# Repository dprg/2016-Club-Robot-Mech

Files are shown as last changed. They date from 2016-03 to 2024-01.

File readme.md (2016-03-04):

# DPRG Club Robot - 2016

This GIT repository contains the design files of the mechanical parts used in DPRG's 2016 version of the club's robot.

The purpose of the robot is to provide a simple, flexible, and sturdy chassis with good components that can grow with the member's skills.

The robot is designed to be able to participate in most of DPRG's indoor competitions. 

The repository includes Inkscape files for laser cut parts, and Design Spark Mechanical and .stl files for 3D printed parts.

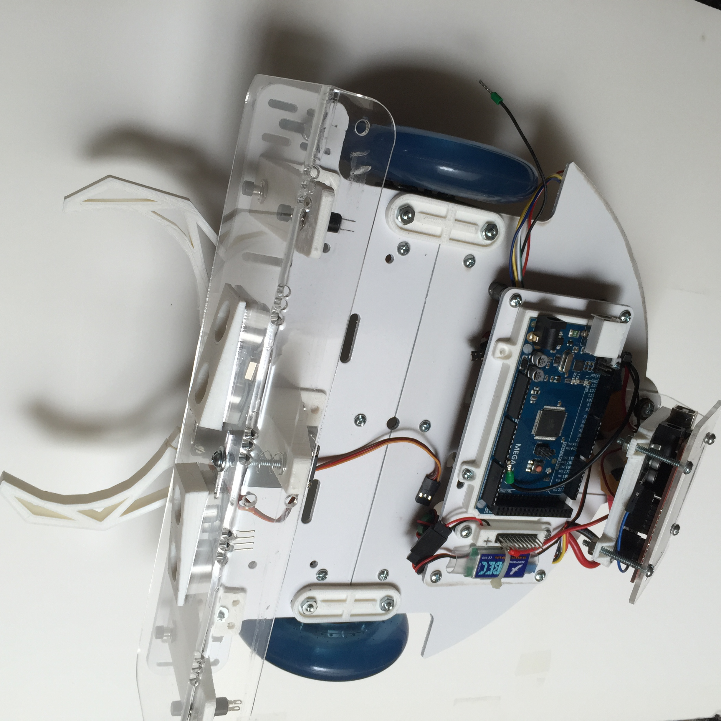
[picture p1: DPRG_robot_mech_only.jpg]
DPRG Robot - Mechanical Parts


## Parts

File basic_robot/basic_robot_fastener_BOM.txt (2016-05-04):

Basic Club Robot (version 2016) Fasteners BOM

Quality     Description
-------    --------------------------
   2       M3-0.5x6mm flat head screws
   2       4-40x3/8" screws
   4       4-40x1/2" Nylon screws
   2       4-40x3/4" screws
  24       6-32x1/2" screws
   9       6-32x3/4" screws
   4       6-32x1"   screws
   3       6-32x1-1/2" screws
   4       6-32x1-1/2 Nylon screws
   1       6-32x2-1/4" screws
   4       8-32x1"   screws
   
   4       4-40 nuts
  47       6-32 nuts
   3       6-32 lock nuts
   4       6-32 Nylon nuts
   4       8-32 nuts
   
   8       #6 washers

3D Printed Hubs

Quality     Description
-------    --------------------------
   6       4-40x3/4" screws
   4       6-32x5/16 set screws

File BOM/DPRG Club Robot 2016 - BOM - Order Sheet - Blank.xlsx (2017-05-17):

BOM for DPRG Club Robot - 2016 |  |  |  | Name -> | <enter your name>
CkBox My Order [x] | Description | Qty | Each | Baseline Cost (all options) | My Order | Comment
 |  |  |  | $196.00 | $178.00
x | Set of laser cut parts | 1 | $6.00 | $6.00 | $6.00
 | (base, motor/wheel, deck, bumper,
 | caster plate, display,
 | stand offs (20))
x | Set of 3D printed parts - PLA | 1 | $8.00 | $8.00 | $8.00
 | (bumper(3), base (2), claw,
 | buss (2), uno plate, mega plate,
 | USB guard, ultrasonic (2), fuse
 | guard, male pin protectors (2),
 | hubs (2))
x | Caster | 1 | $4.00 | $4.00 | $4.00
x | Screw/nut set | 1 | $6.00 | $6.00 | $6.00
x | Bumper springs | 2 | $1.00 | $2.00 | $2.00
x | Priming of base & deck parts | 1 | $3.00 | $3.00 | $3.00 | optional
x | Bumper switches - NC | 4 | $0.50 | $2.00 | $2.00
x | On/Off switch | 1 | $1.00 | $1.00 | $1.00
x | Wheels - 100 mm | 2 | $4.00 | $8.00 | $8.00
x | Pololu Hubs | 2 | $5.00 | $10.00 | $10.00 | optional
x | Motors with encoders | 3 | $10.50 | $21.00 | $31.50 | indicate speed (100 RPM or 200 RPM)
 | ( std - 100 RPM @ 6V) |  |  |  |  | 100 RPM
 | ( fast - 200 RPM @ 6V)
x | Set of jumpers - Dupont plugs | 1 | $6.00 | $6.00 | $6.00
 | (mix of m/m, m/f, f/f)
x | Misc wire | 1 | $1.00 | $1.00 | $1.00
x | Terminals - double row, 100 mil | 2 | $1.00 | $2.00 | $2.00
x | UBEC – 5V | 1 | $6.00 | $6.00 | $6.00
x | XT60 terminal set - m & f | 2 | $1.00 | $2.00 | $2.00
x | Resettable Fuse - 5A PPTC | 1 | $1.00 | $1.00 | $1.00
x | 2.4" TFT Display Shield | 1 | $6.00 | $6.00 | $6.00
x | Ultrasonic sensors - HC-SR04 | 2 | $1.00 | $2.00 | $2.00
x | IR sensor - non-modulated | 2 | $1.00 | $2.00 | $2.00
x | IR sensor – modulated | 3 | $2.00 | $6.00 | $6.00
x | Hobby servo - std size | 1 | $6.00 | $6.00 | $6.00
x | MonsterMoto motor driver clone | 1 | $10.00 | $10.00 | $10.00
x | Arduino power plug | 1 | $1.00 | $1.00 | $1.00
x | Arduino Uno clone | 1 | $6.50 | $6.50 | $6.50
x | Arduino Mega2560 clone | 1 | $11.00 | $11.00 | $11.00 | or Nucleo
 | Nucleo STM32F411 | 1 | $11.00 | $11.00 | $0.00 | or Mega
x | Battery LiPo - 11.1V, 2.2KmAh | 1 | $16.00 | $16.00 | $16.00 | or NiMH
 | Battery NiMH - 9.6V, 2.2KmAh | 1 | $17.50 | $17.50 | $0.00 | or LiPo
x | Nucleo Breakout board and parts | 1 |  |  | $0.00
 | (designed by Ron Grant)
x | PayPal Fees | 1 | $2.00 | $2.00 | $2.00
x | Contingency Fund | 1 | $10.00 | $10.00 | $10.00
 | (shipping, unexpected price change)

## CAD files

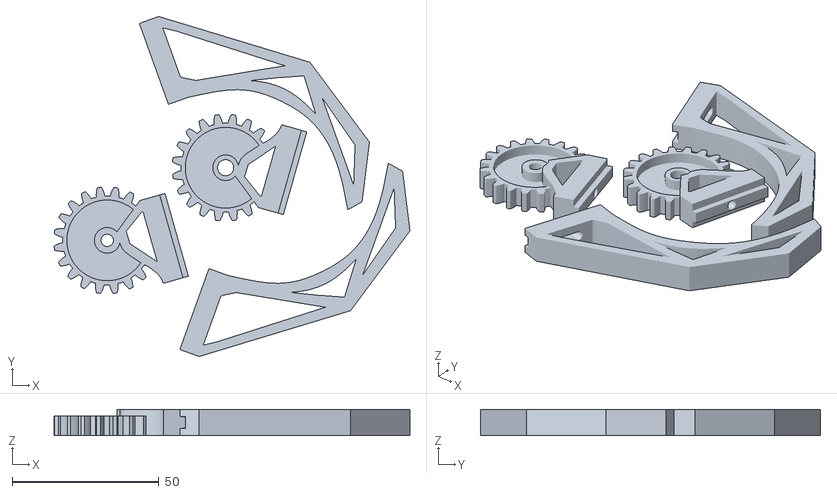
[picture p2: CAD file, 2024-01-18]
basic_robot/3d_print_parts/robot_claw_revised-1.stl
121.3 x 115.9 x 9.00

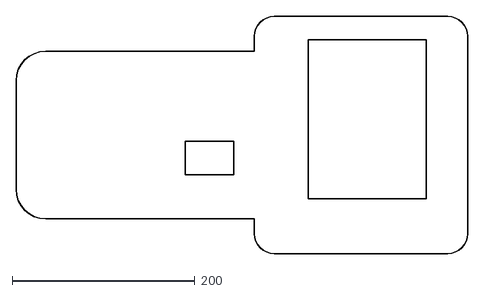
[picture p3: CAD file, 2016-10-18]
basic_robot/laser_cut_parts/display_support.dxf
494.2 x 259.4

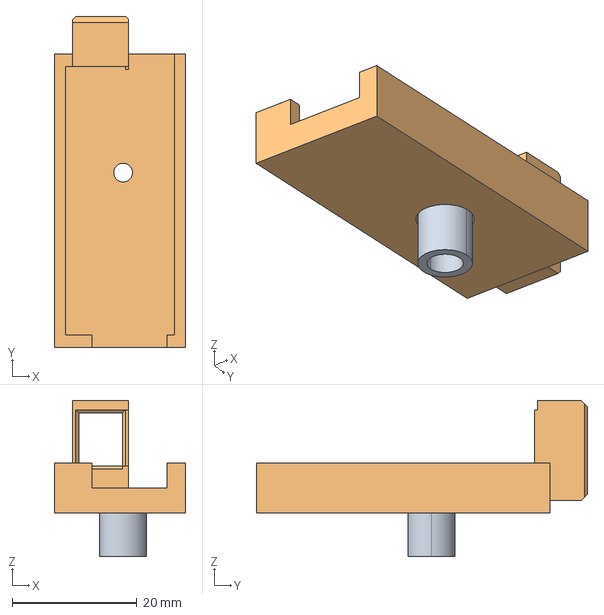
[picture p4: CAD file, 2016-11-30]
optional_parts/3d_print_parts/KeyesIr_Mount.stp
21.0 x 53.0 x 25.0 mm
Mount
Platform

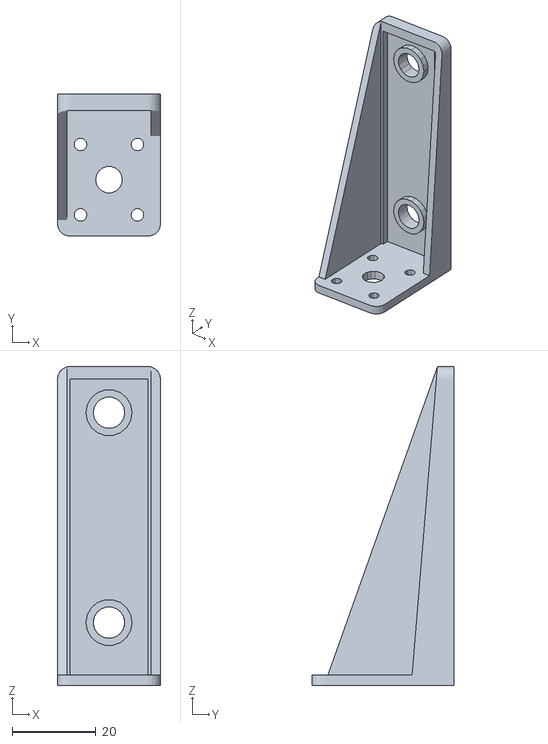
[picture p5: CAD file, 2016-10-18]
basic_robot/3d_print_parts/bumper_switch_support_left.stl
24.6 x 33.9 x 76.0

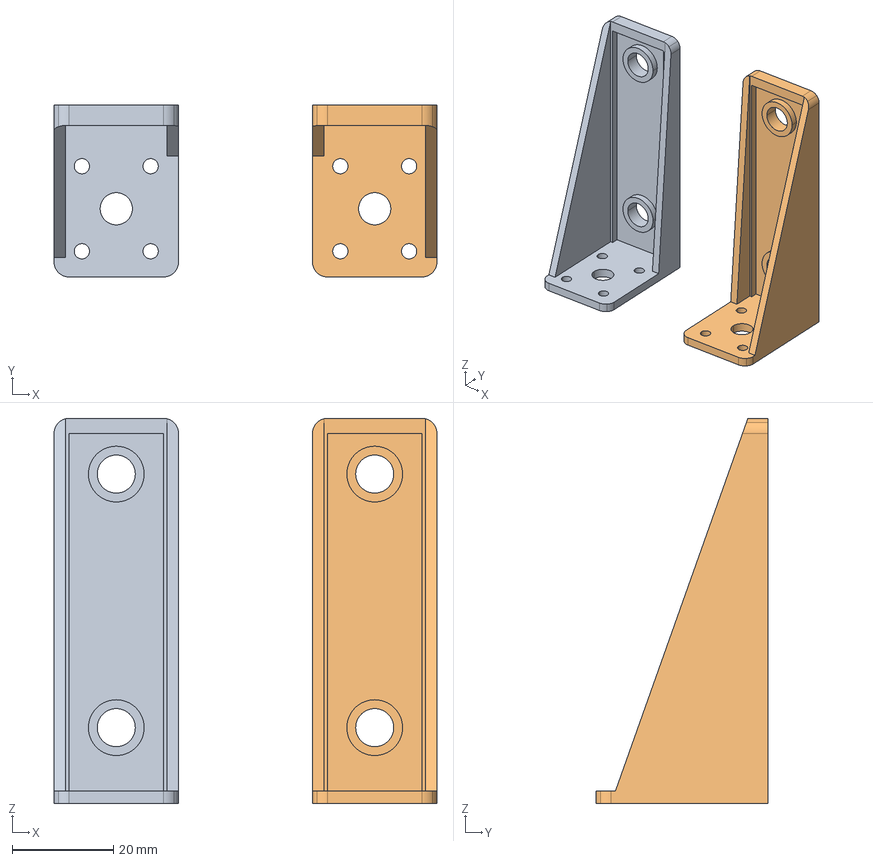
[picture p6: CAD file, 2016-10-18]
basic_robot/3d_print_parts/bumper_switch_support.stp
75.5 x 33.9 x 76.0 mm
Left
Right

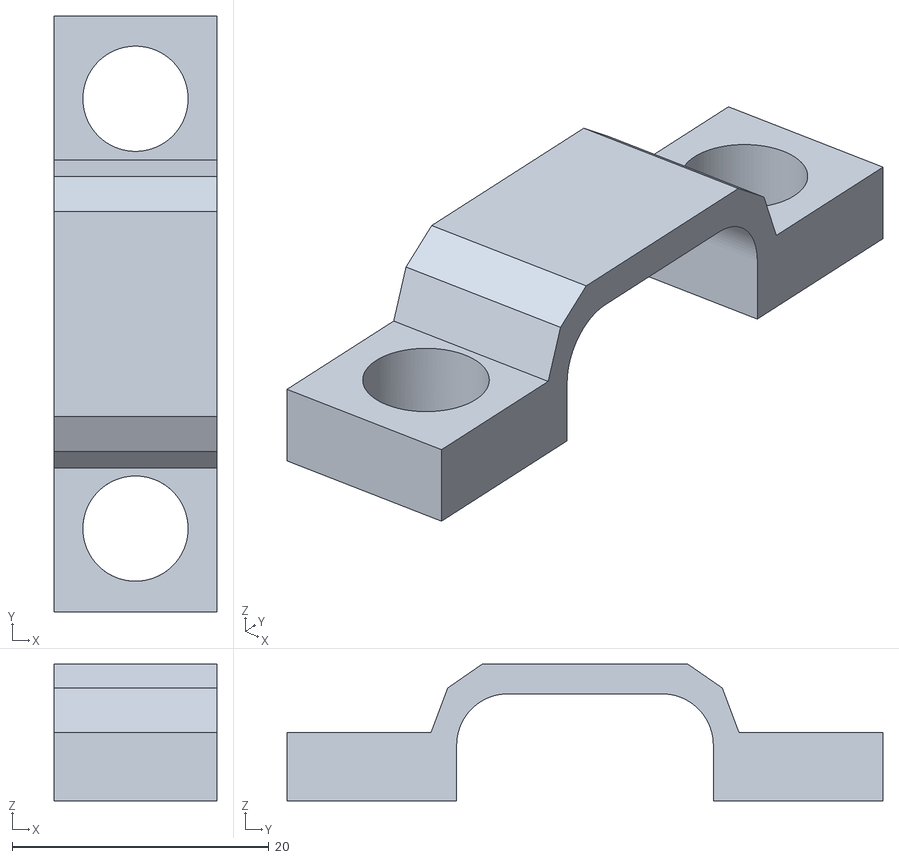
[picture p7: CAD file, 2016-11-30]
optional_parts/3d_print_parts/xt60_hold_down.stl
12.7 x 46.4 x 10.7

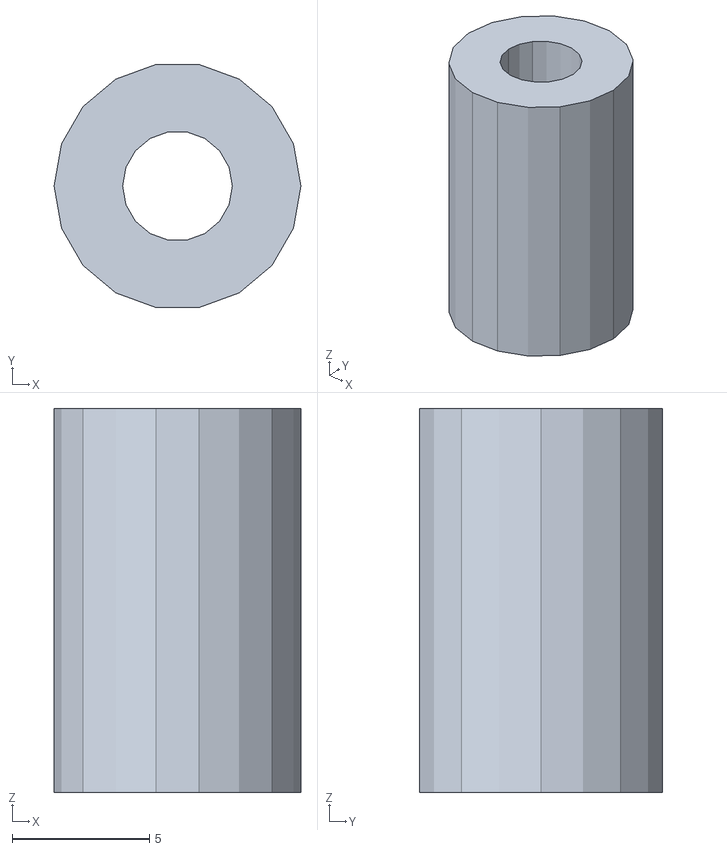
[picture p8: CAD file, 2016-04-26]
basic_robot/3d_print_parts/spacer-14mm.stl
9.00 x 8.86 x 14.0

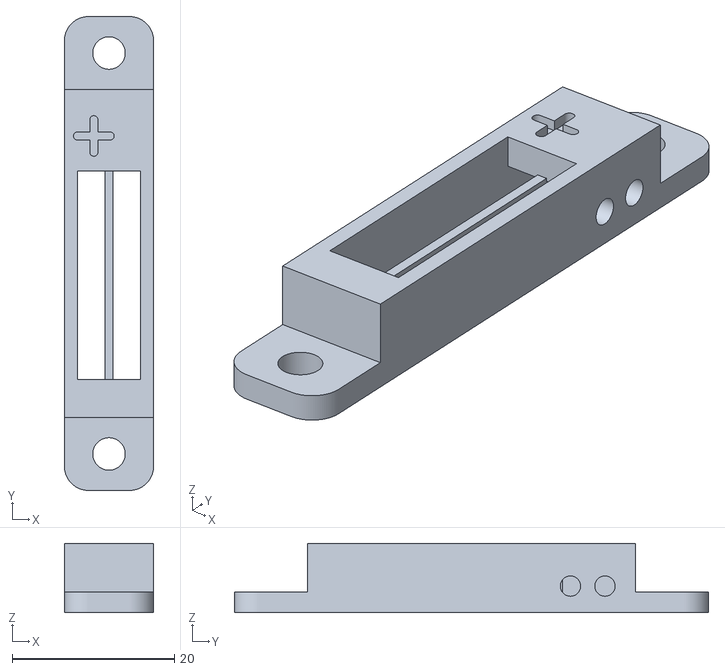
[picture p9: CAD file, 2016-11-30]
optional_parts/3d_print_parts/alternate_buss_block.stl
11.0 x 58.4 x 8.50

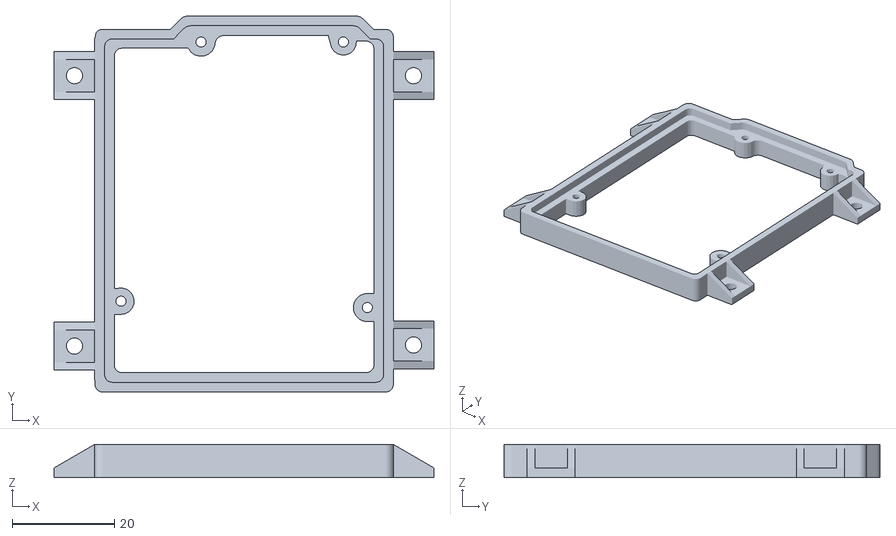
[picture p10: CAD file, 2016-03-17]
basic_robot/3d_print_parts/uno_mount.stl
74.4 x 73.7 x 6.50

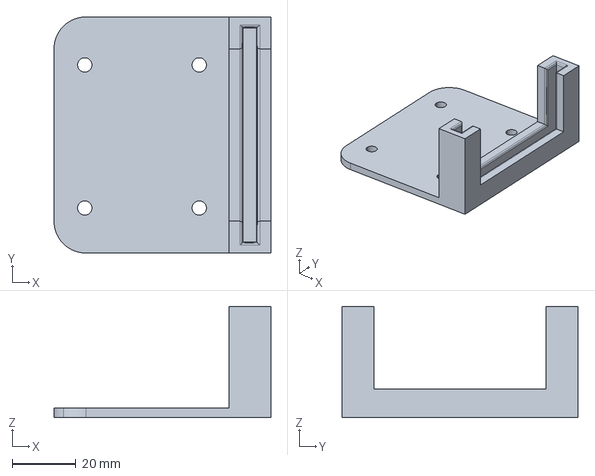
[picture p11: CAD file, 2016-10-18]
optional_parts/3d_print_parts/AlternateDisplayHolder.stp
68.2 x 74.2 x 35.0 mm

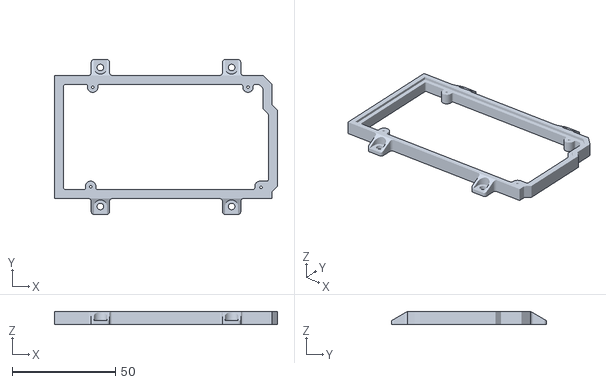
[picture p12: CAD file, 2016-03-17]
basic_robot/3d_print_parts/mega_mount.stl
107.9 x 74.9 x 6.35

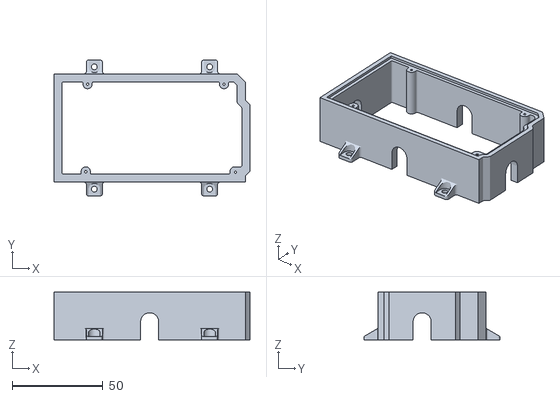
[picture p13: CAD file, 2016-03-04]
optional_parts/3d_print_parts/mega_mount-tall.stl
107.9 x 74.9 x 26.4

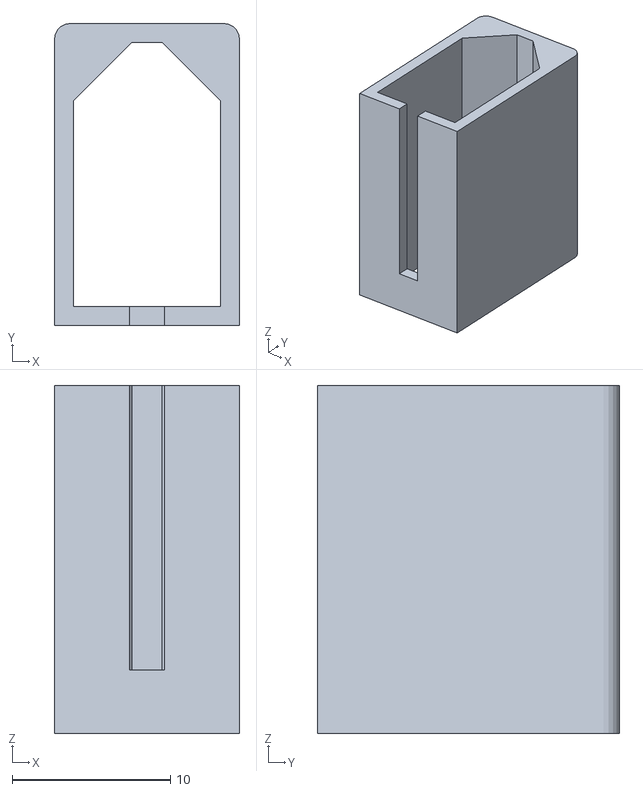
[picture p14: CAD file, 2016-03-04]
basic_robot/3d_print_parts/fuse_cover.stl
11.7 x 19.1 x 22.0

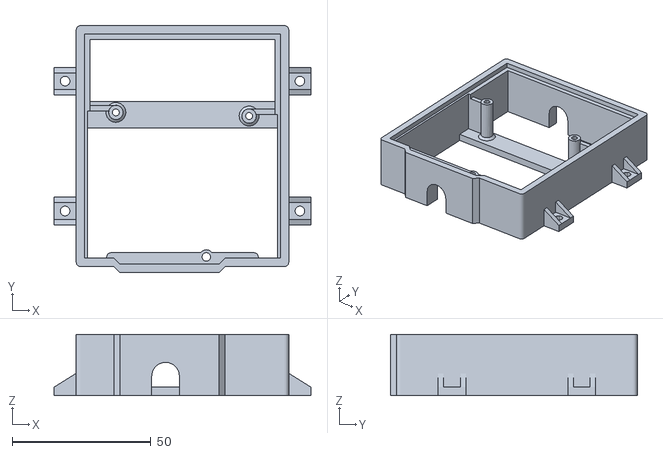
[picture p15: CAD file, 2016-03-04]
optional_parts/3d_print_parts/Nucleo_mount.stl
92.6 x 88.9 x 22.0

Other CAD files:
basic_robot/3d_print_parts/bumper_switch_support_right.stl
optional_parts/3d_print_parts/alt_bumper_switch_support_left.stl
optional_parts/3d_print_parts/alt_bumper_switch_support_right.stl
basic_robot/3d_print_parts/robot_claw.stl
basic_robot/3d_print_parts/Dupont_connector_sleve.stl
basic_robot/3d_print_parts/USB_cover.stl
basic_robot/3d_print_parts/base_plate_stiffer.stl
basic_robot/3d_print_parts/bumper_spring_ctr_post.stl
basic_robot/3d_print_parts/bumper_switch_support.stl
basic_robot/3d_print_parts/buss_block.stl
basic_robot/3d_print_parts/claw_spacer.stl
basic_robot/3d_print_parts/spacer-for_8-32_screw-6_5mm.stl
basic_robot/3d_print_parts/ultrasonic_holder.stl
basic_robot/3d_print_parts/wheel_adpter_hub.stl
basic_robot/3d_print_parts/wheel_adpter_washer.stl
optional_parts/3d_print_parts/AlternateDisplayHolder.stl
optional_parts/3d_print_parts/KeyesIr_Mount(2).stl
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

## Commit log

2016-03-04 DPRG Club Robot - 2016 Design files for laser cut and 3D printed parts.
    [Dupont_connector_sleve.stl, Nucleo_mount.stl, USB_cover.stl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]
2016-03-13 Added screw holes to front and rear base parts to allow for a second deck. Moved Branding from rear base to separate file in optional parts.
2016-03-17 Added low profile Arduino mounts.
    [mega_mount.stl, uno_mount.stl]
2016-04-21 The thickness of the material used for the wheel assembly impacts the dimensions of the individual parts. The most common thicknesses of hardboard are 100mils and 120mils. Select the file that matche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
2016-04-21 Removed wheel_assem.svg which was the same as wheel_assem-100mm.svg.
2016-04-26 3D printed spacer to replace laser cut washers.
    [spacer-14mm.stl]
2016-05-04 add fastener BOM
2016-05-04 Added caster spacer to level robot
    [spacer-for_8-32_screw-6_5mm.stl]
2016-05-04 lengthened screw holes past nut
2016-05-10 motor and encoder info
2016-05-10 fix motor information pdf
2016-10-18 Adding alternate DisplayHolder and BumperSwitch supports
    [AlternateDisplayHolder.stl, AlternateDisplayHolder.stp, bumper_switch_support.stl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]
2016-11-01 Alternate Display and Bumper Support
    [AlternateDisplayHolder.stl, alt_bumper_switch_support_left.stl, alt_bumper_switch_support_right.stl]
2016-11-23 alternate buss block and new hold down clip for fuse block
    [alternate_buss_block.stl, xt60_hold_down.stl]
2016-11-30 moving alternate parts to correct folder
    [AlternateDisplayHolder.stl, alt_bumper_switch_support_left.stl, alt_bumper_switch_support_right.stl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]
2016-11-30 moving alt buss block to correct folder
    [alternate_buss_block.stl]
2016-11-30 KeyesIR Mount
    [KeyesIr_Mount(2).stl, KeyesIr_Mount.stl, KeyesIr_Mount.stp]
2016-11-30 moving Alt Display holder to correct folder
    [AlternateDisplayHolder.stl, AlternateDisplayHolder.stp]
2017-05-17 Added baseline BOM - still needs sourcing info...
    [DPRG Club Robot 2016 - BOM - Order Sheet - Blank.xlsx]
2024-01-18 Add files via upload
    Removed unused solids from robot claw model.
    [robot_claw_revised-1.stl]
